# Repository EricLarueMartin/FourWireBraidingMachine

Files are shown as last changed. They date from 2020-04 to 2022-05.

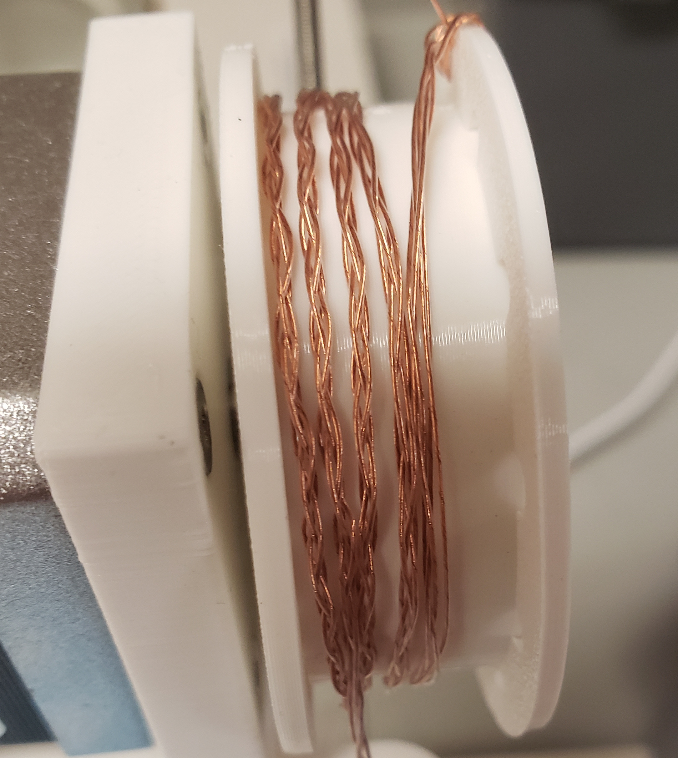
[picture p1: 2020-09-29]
Documentation/NoKinks.jpg

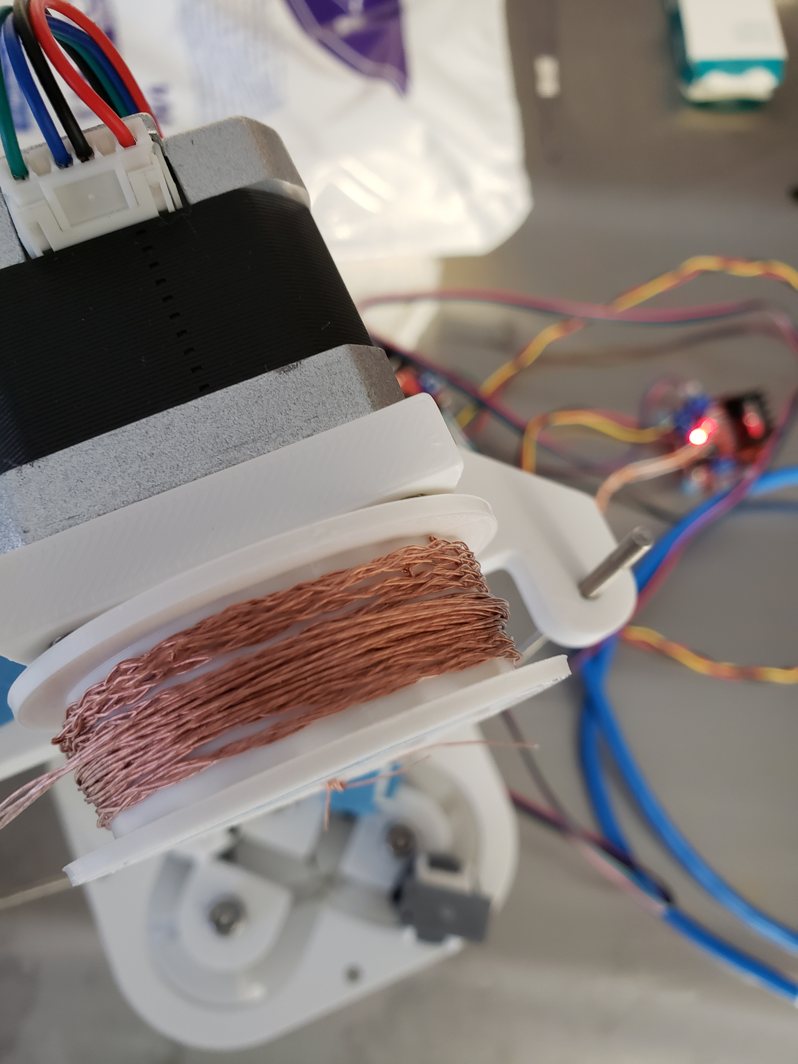
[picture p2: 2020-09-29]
Documentation/20200612_144232 1.jpg

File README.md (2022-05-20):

# FourWireBraidingMachine
Four wire braiding machine constructed out of widely available or printed parts.

Uses four horn gears to move four spool holders around on carriages. 
Design files for inventor included. Design could easily be extended for larger number of wires.

In addition to printed parts the following will be needed:

NEMA 17 stepper motors and drivers (L298N stepper motor driver boards were used, but anything compatible with Arduino is fine)

Arduino (Arduino Leonardo was used, but any Arduino is fine)

608 bearings (standard roller skate or skateboard bearings)

M8 threaded rod

M8 lock nuts (jam nuts could also be used)

M3 partially threaded bolts (for spool shaft)

M3 flathead bolts (must be flathead for gears to pass over bolt)

M3 threaded rods

M3 lock nuts (jam nuts could also be used)

Spring for clutch, SP-9702 was used but anything that fits and isn't too strong should work.

Spring for tips, 152-B from W.B. Jones Spring Co was used. Many other springs were found to work, but this is less tolerant than the clutch as it can't be adjusted.

**Ultem parts for ultra clean braiding:**

For the spools that go around the track:

4x SpoolHolderGuide

4x SpoolHolderRiser

4x SpoolSinglePieceTraditionalMachining — this is a remake of Spool designed for traditional machining.

For the winder:

1x WinderBracketInsert

1x WinderSpoolSinglePieceTraditionalMachining — this is a remake of WinderSpool designed for traditional machining.

When using the braider with Ultem parts print WinderBracket without the insert. WinderBracket and WinderBracketInsert can be printed as a single piece if not using a clean insert.

This design is free to use under the Creative Commons license. https://creativecommons.org/licenses/by-nc-sa/4.0/

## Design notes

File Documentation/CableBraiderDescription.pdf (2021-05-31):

## Non-twisting Cable Braider

### Eric L. Martin

09/20/20

A non-twisting cable braider was designed for braiding the signal cables for the LEGEND experiment, which requires very low-noise signal transmission. The area between cables acts as an antenna, picking up noise proportional to the area enclosed by the cables from ambient electromagnetic radiation. Two methods of reducing pickup noise used by LEGEND are braiding cables and shielding cables. By braiding the cables alternating loops are formed, which will have alternating polarity of pickup noise from loop to loop. This causes signicant cancellation of pickup noise. Smaller loops formed by twisting the cable tighter tends to provide better noise reduction, and has the added benet of producing an easier to handle cable bundle. Shielding the signal conductor with a grounded shield also reduces pickup noise, but there is always some noise that makes it through the shieldespecially at low frequency where the skin depth is longer than shield thickness. In bundles of shielded cables, the shields themselves also become antenna loops and this pickup can be mitigated by braiding the cables. LEGEND is testing braided bundles of individually shielded coaxial cables.
The LEGEND cable braider uses spools on carriages that are moved around a track by horn gears. As it is weaved the nished cable is wound on another spool, and the relative speed at which the cable is wound compared to how frequently the spool carriages move around the track controls the braid pitch. Cable braiders employing spools being moved around a track by horn gears have been used for more than a century. The most popular type is a maypole pattern, formed by two groups of cable carriers moving in opposite directions around a rough circle. The carriers switch between the inside and outside track to weave a tube around the center. Another method is to pass pairs of cables through the center of the cable braid, cycling through pairs of cables. Such a design was patented in 1989 under US patent 4803909. When braiding only four cables, such as will be done for LEGEND, this pattern is identical to a maypole braiding pattern. If additional spools are added to the LEGEND braider it will closely resemble the 1989 design, but with a key improvement to preventing twisting the cables. Braiding the LEGEND signal cables on a machine similar to the 1989 style of braiding machine resulted in either braids with too long a braid pitch to be easily handled, or kinks in the braided cable as shown in gure 3.
As the spools are moved around the track they rotate one revolution per

1

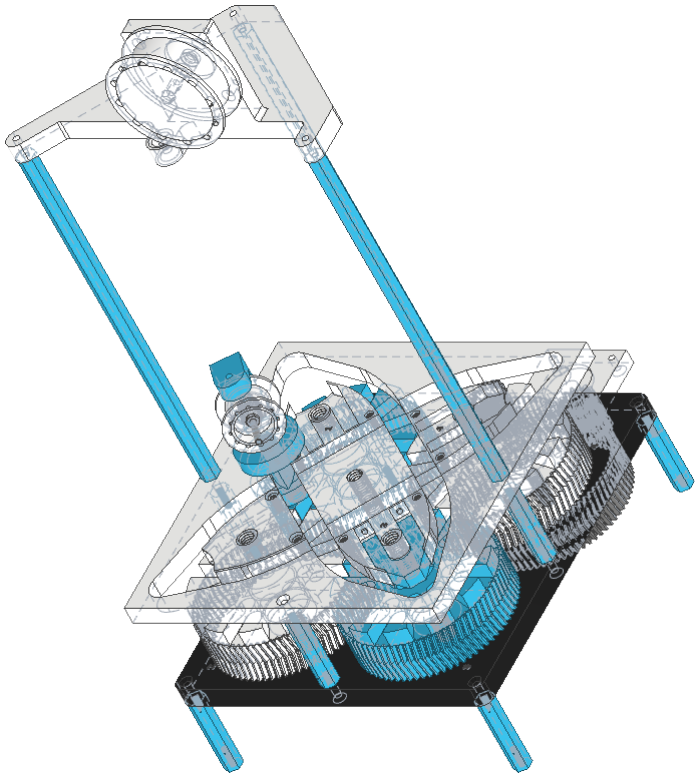
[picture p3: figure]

Figure 1: Non-twisting cable braider. Shown with one spool assembly, one spring tip on the lower right, and one tip cover on the lower left. Shafts, springs, motors, and most fasteners not shown.

2

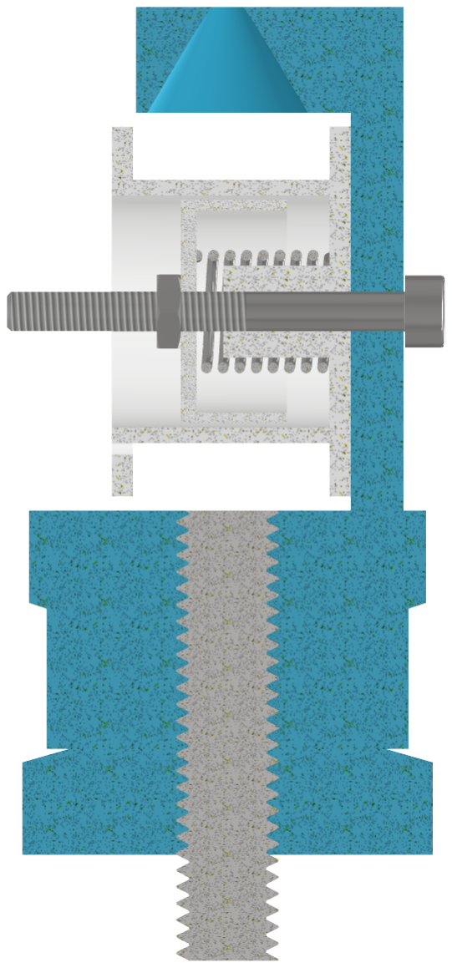
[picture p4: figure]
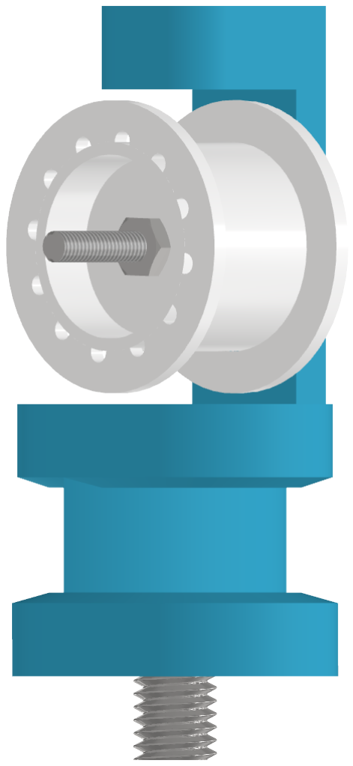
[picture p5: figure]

Figure 2: A spool assembly, half section view on the right. Cable is wound around the spool and the free end is threaded through the hole in the top of the spool holder. The spool rotates around a horizontal axle, this way no twisting of the cable occurs from unwinding the cable from the spool. The spring around the spool axle held by a bushing positioned by a lock nut applies force on the spool against the rising arm of the spool holder. Moving the lock nut adjusts the tension of the spool to prevent it from unwinding freely. An alternate design with a rewinder was considered to take up slack as the spool traveled through the central area of the track, but the slack didn't cause any issues so this simple friction clutch was used.

3

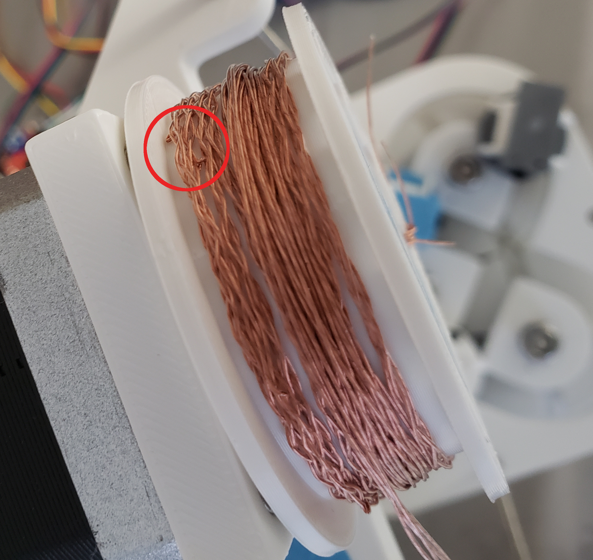
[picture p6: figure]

Figure 3: Kinks occurred when tightly braiding the LEGEND signal cables using a braiding machine that would twist the cables. Two such kinks are circled in red. Also shown on the spool is a section of cable that was braided with a longer braid pitch. While the longer braid pitch prevented kinks, the cable was dicult to handle.

4

trip around the track, twisting the cable once. This can be compensated for by taking the cable o the end results in one twist per loop removed from the spool. If the spools are wound such that the twist from cable coming o the spool cancels the twist from traversing the track there is no resulting twist in the cable. However, this requires the circumference of the spool matches the braid pitch. This would require a tightly wound spool for a tight cable braid, limiting the braid pitch by the minimum bending radius of the cable. This approach to eliminating cable twisting was unsuitable for attaining the high braid pitch desired for LEGEND.
To achieve a high braid pitch two improvements were made to the cable braider over the initial design.
Most importantly, the spools were oriented so cable was taken from the side instead of the end, so that there was no twisting induced by unwinding the cable from the spool (see gure 2). The track was redesigned to compensate for rotation of the spool as it traveled around the track (see gure 4). This counter rotation was induced by recesses added to the track. The recesses would catch the carriage guides and rotate the spools to compensate for the rotation due to movement around the track. Adding a retractable part of the track that the guide can push aside was found most eective, but rotation can be induced using a xed track with only recesses.
The second improvement was to shift the position of the spool carriages on the horn gears. In the previous design the slots in the horn gears were symmetric, causing two spools to be in the same position on opposite sides of the track. The carriages experience some positions of higher resistance, the most noticeable for the non-twisting cable braider is when pushing on the retractable track section. By shifting the spool positions (see gure 6) the machine only has to push a spool carriage through these dicult points one at a time instead of two at a time, reducing the torque required by the motor and allowing the machine to run faster. Breaking the symmetry of the track would have accomplished this as well but would have been more complicated.

5

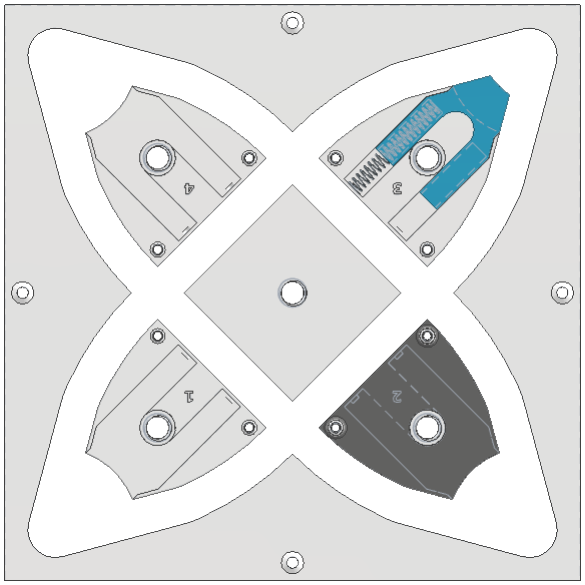
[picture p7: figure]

Figure 4: Track with rotation countering recesses at turning points. Only one of the spring-loaded retractable tips is shown in blue in the upper right, and only one cover is shown installed in gray in the lower right.

6

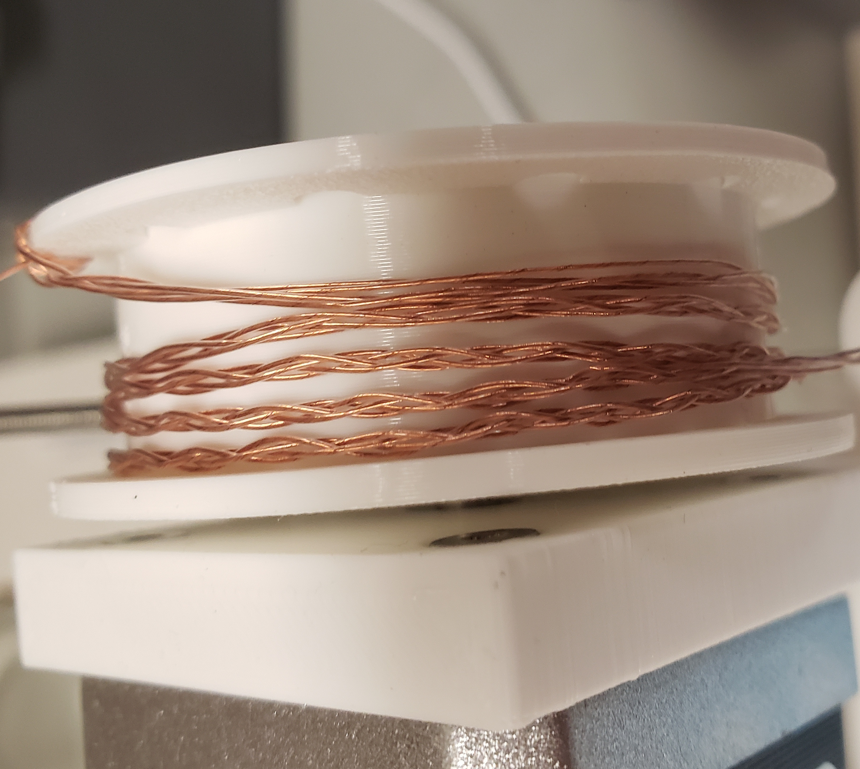
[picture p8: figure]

Figure 5: The same cable as in gure3 rebraided with the non-twisting cable braider.

7

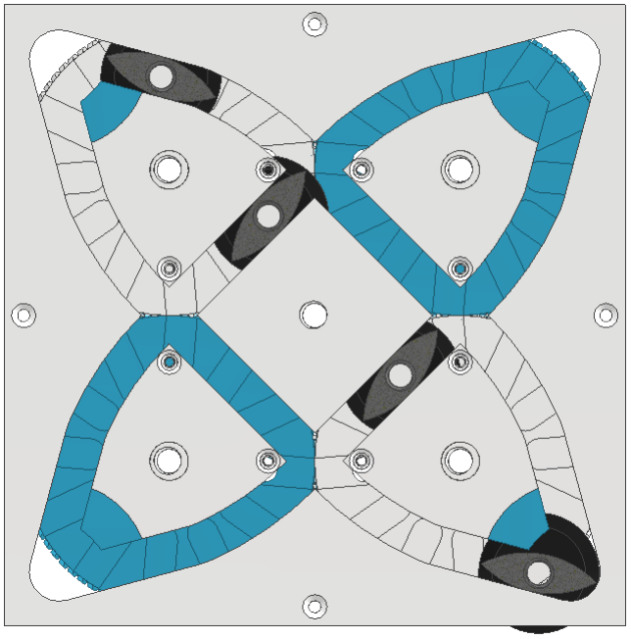
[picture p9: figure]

Figure 6: Additional slots were added to the horn gears to allow osetting the spools, so no more than one spool at a time passed the same problem point in the track. Preventing two spools from passing the rotation compensating corners at the same time is most important, as that is the highest resistance point in the movement. The carriage guide portion of the spool assemblies are shown in gray.

8

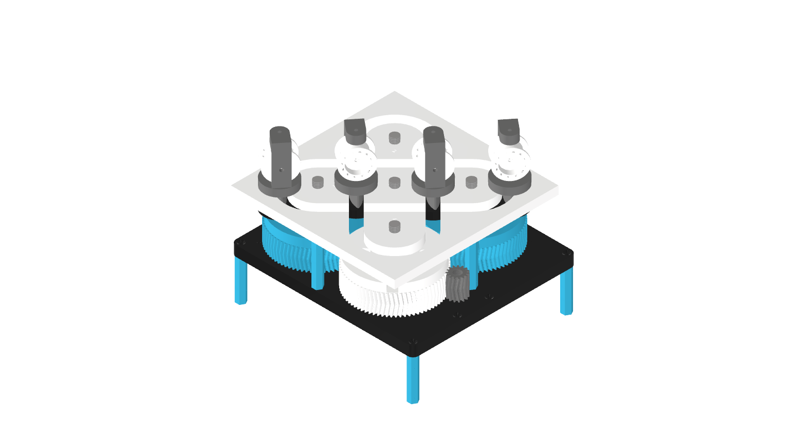
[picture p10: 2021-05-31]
Documentation/CableBraiderTwisting.png

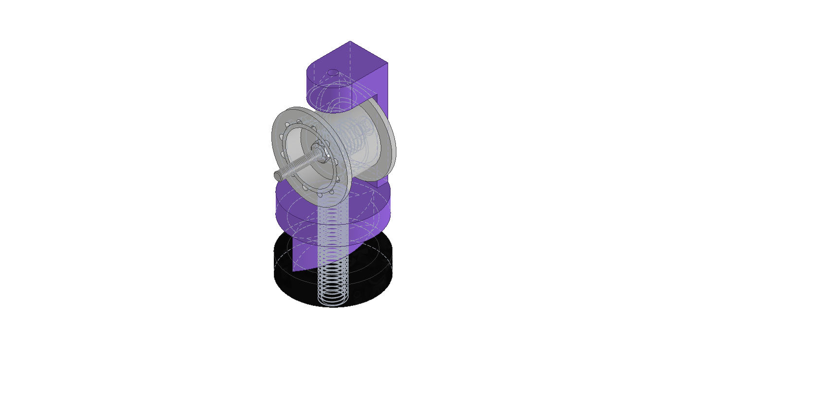
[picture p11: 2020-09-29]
Documentation/Carriage.png

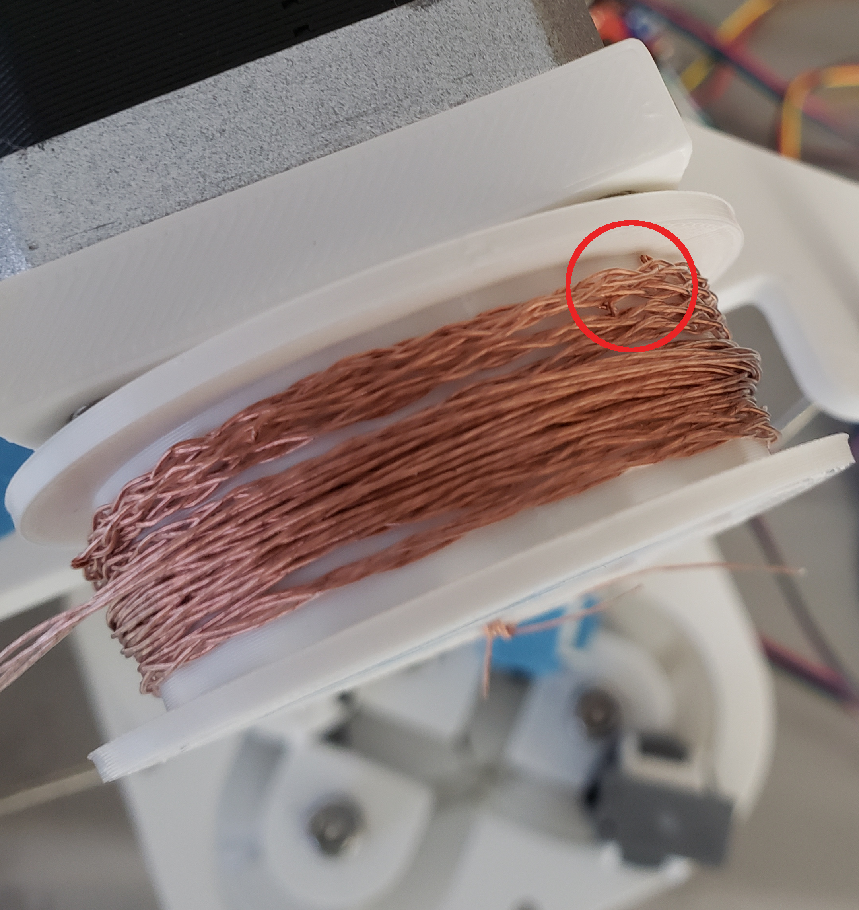
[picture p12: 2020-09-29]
Documentation/Kinks.jpg

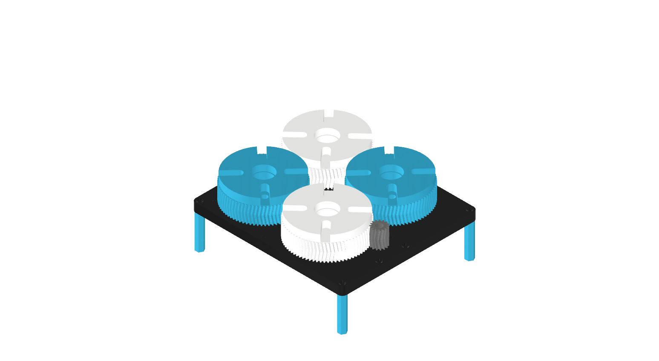
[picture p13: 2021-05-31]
Documentation/CableBraiderTwistingGears.png

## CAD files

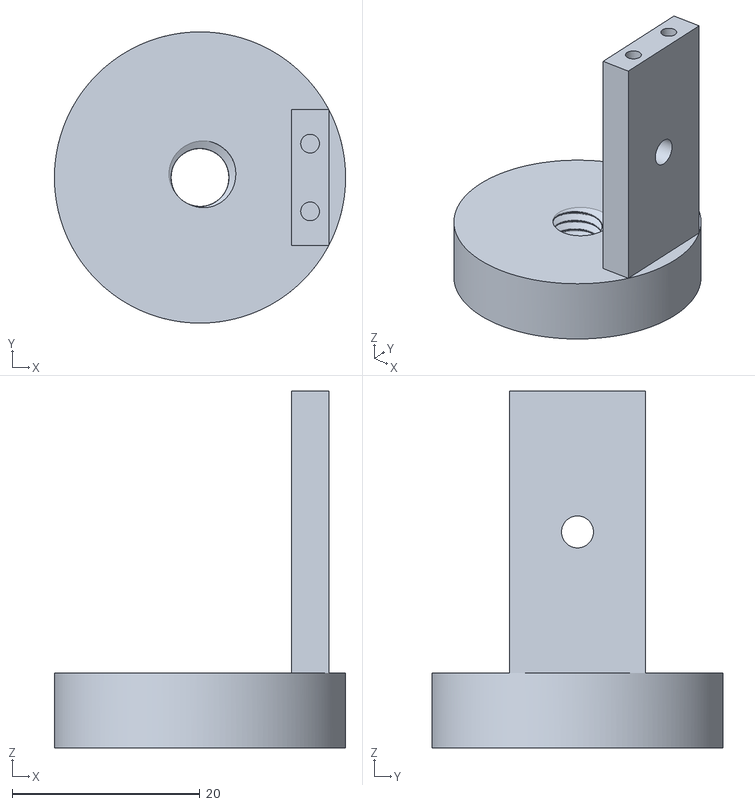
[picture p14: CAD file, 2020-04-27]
InventorFiles/SpoolHolder.stl
31.0 x 31.0 x 38.0

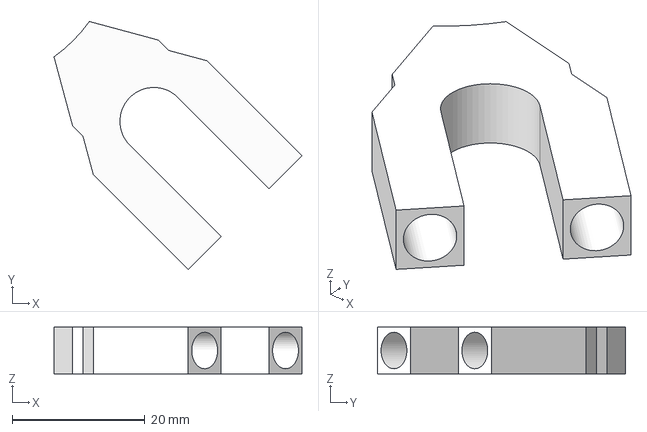
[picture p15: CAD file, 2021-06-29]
MetalPartStepFiles/GuidePlateTip.stp
37.3 x 37.3 x 7.00 mm

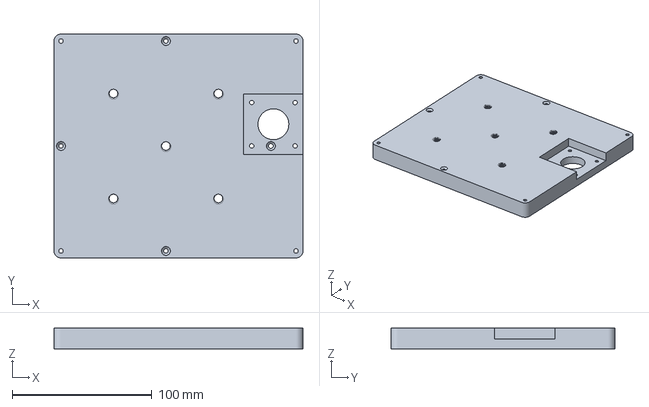
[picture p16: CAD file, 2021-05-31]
PrintingFiles/BasePlate.3mf
177.9 x 160.0 x 15.0 mm

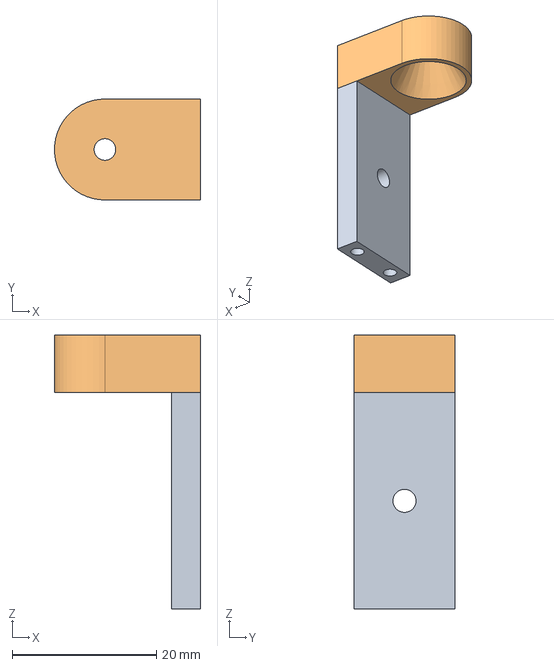
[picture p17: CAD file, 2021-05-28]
SpoolHolderRiserAndGuide.stp
20.3 x 14.0 x 38.0 mm

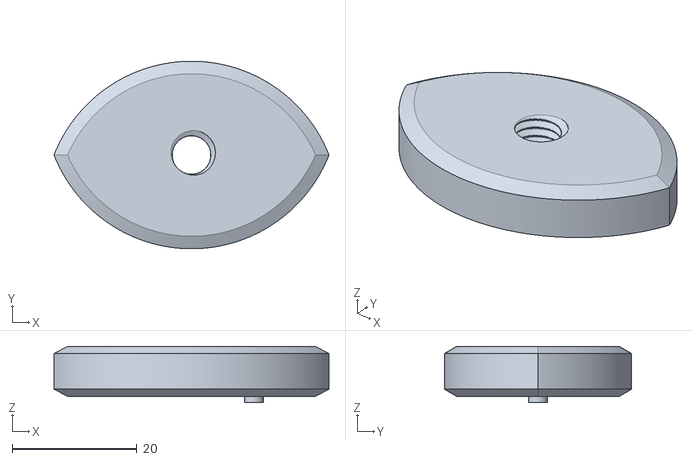
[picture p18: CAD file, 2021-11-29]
STLfiles/CarriagePlate.stl
44.0 x 30.0 x 9.00

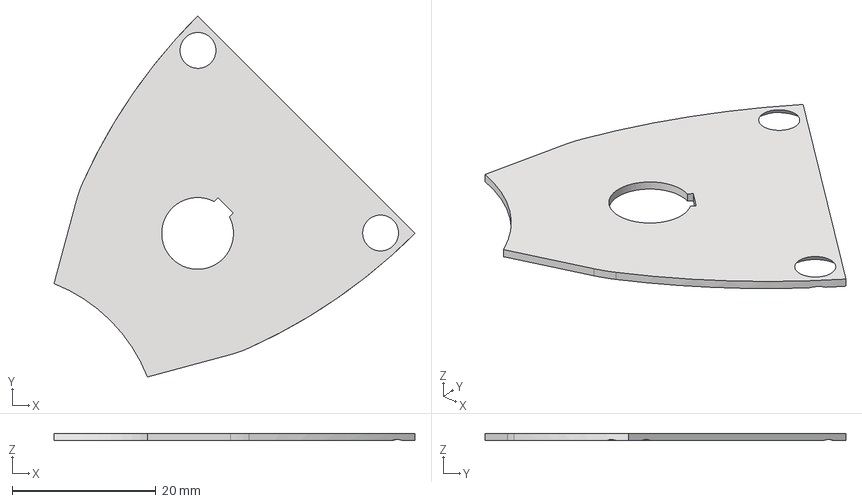
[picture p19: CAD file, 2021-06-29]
MetalPartStepFiles/GuidePlateCover.stp
50.3 x 50.3 x 1.00 mm

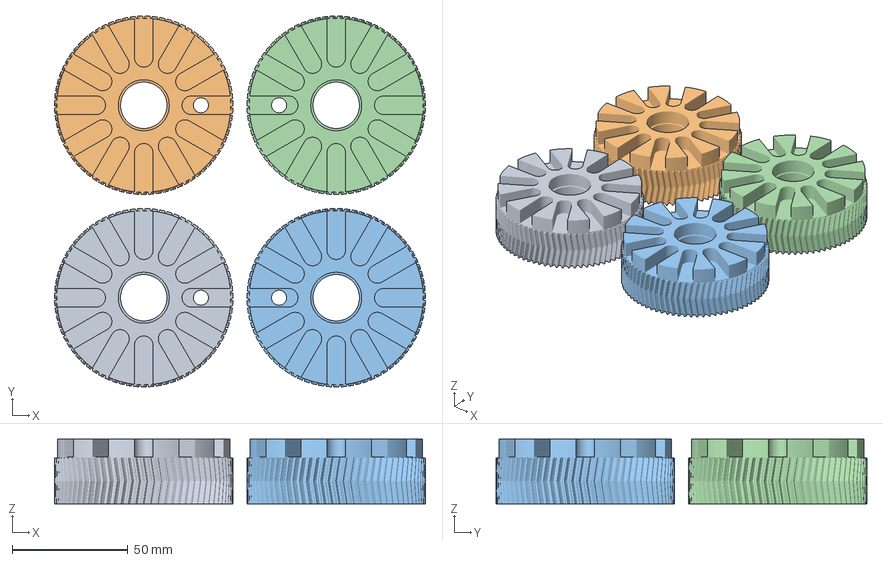
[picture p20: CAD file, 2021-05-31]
PrintingFiles/HornGearsMod1.3mf
160.0 x 160.0 x 28.0 mm
HornGearMod1.stl x 2

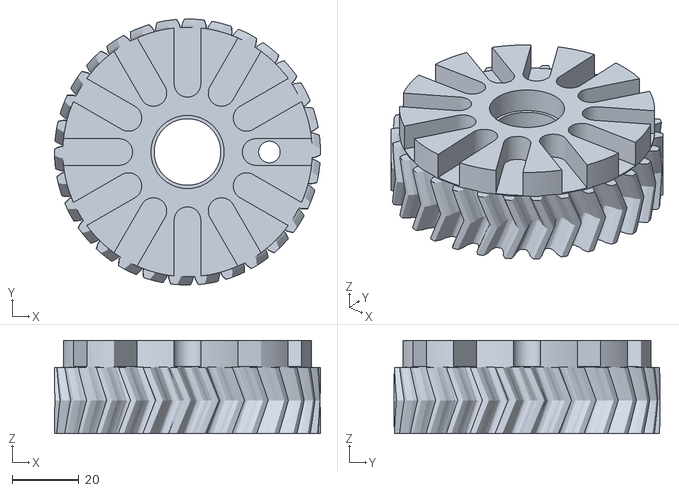
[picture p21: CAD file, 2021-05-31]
STLfiles/HornGearMod2.5.stl
80.0 x 80.0 x 28.0

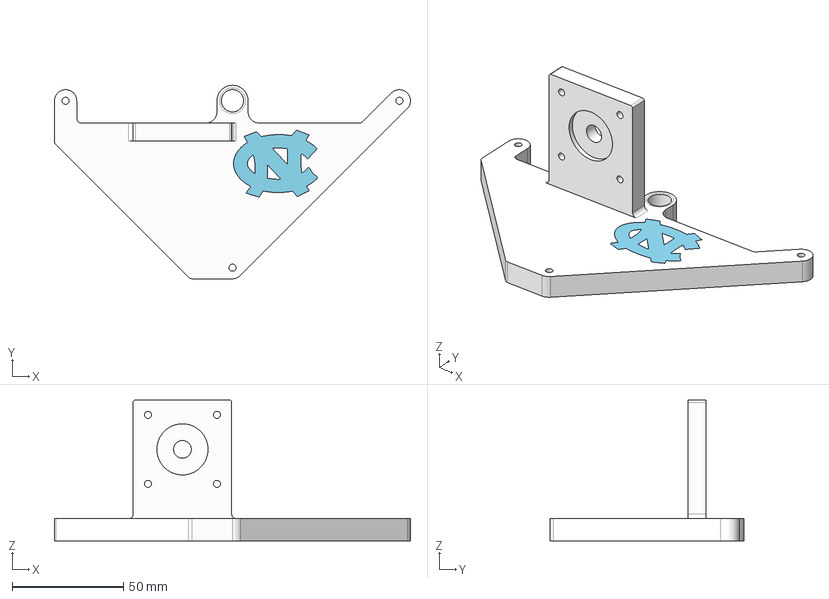
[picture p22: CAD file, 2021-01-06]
WinderBracket.stp
160.0 x 87.0 x 63.3 mm

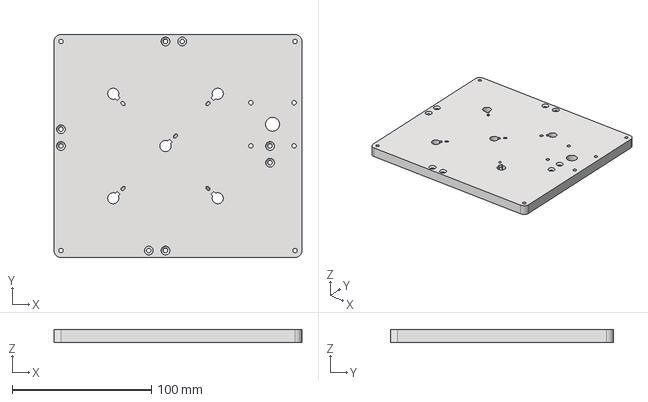
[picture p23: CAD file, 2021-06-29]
MetalPartStepFiles/BasePlate.stp
177.9 x 160.0 x 9.00 mm

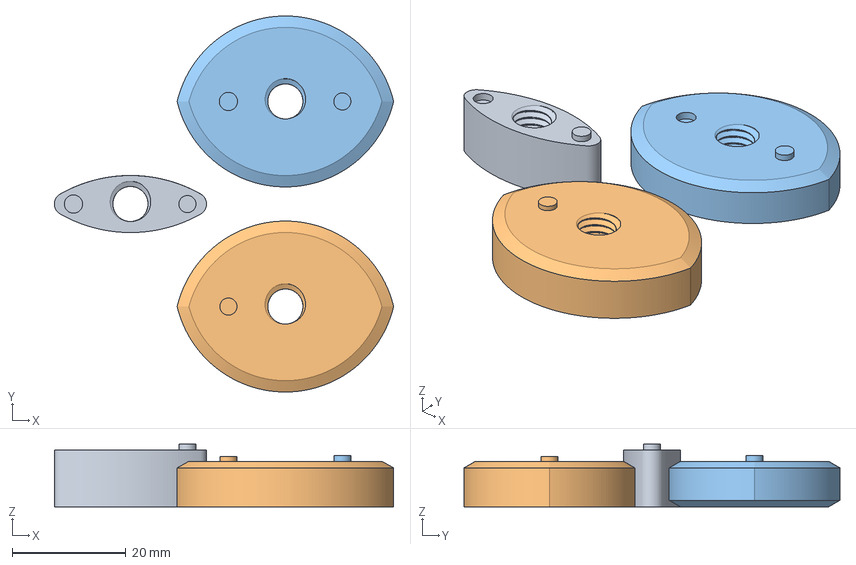
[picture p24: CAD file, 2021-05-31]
PrintingFiles/ThreePieceSpoolCarriageBase.3mf
59.6 x 66.0 x 11.0 mm
SpoolHolderGuide.stl
SpoolHolderBase.stl
CarriagePlate.stl

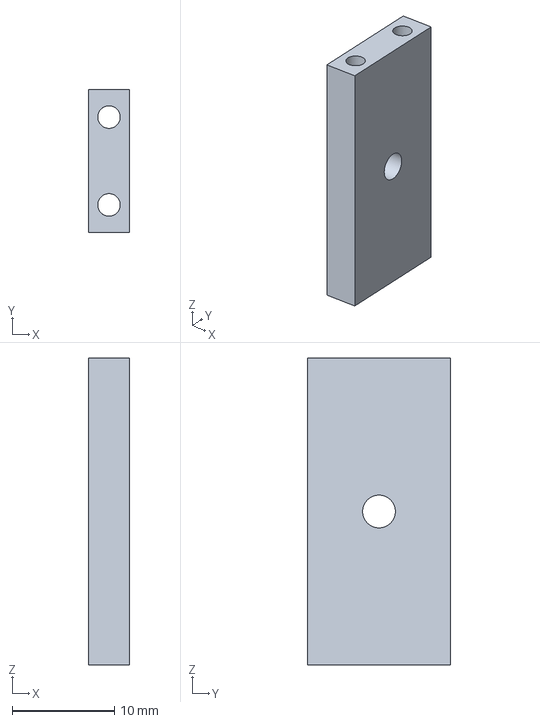
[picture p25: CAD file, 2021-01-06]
SpoolHolderRiser.stp
4.00 x 14.0 x 30.0 mm

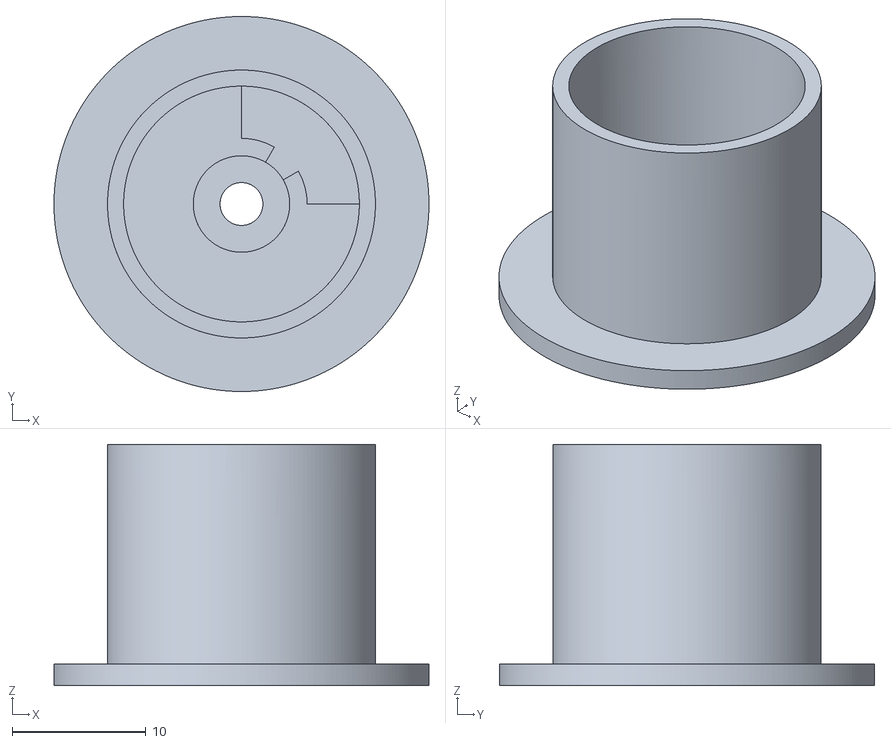
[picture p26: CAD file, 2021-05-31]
STLfiles/RewindingSpool.stl
28.0 x 28.0 x 18.0

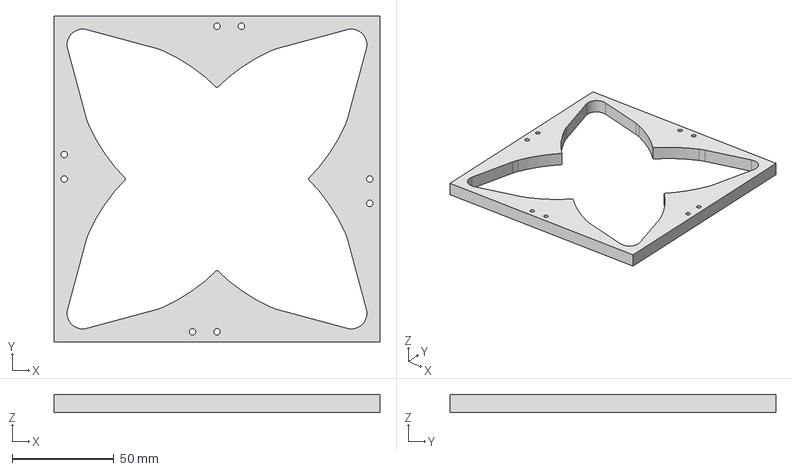
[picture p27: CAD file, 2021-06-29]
MetalPartStepFiles/GuidePlateOuter.stp
160.0 x 160.0 x 9.00 mm

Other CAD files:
PrintingFiles/BasePlateMetal.3mf
STLfiles/GuidePlateV1Center.stl
WinderBracketInsert.stp
MetalPartStepFiles/HornGearShaft.stp
Documentation/GuideDemo.iam
Documentation/OldVersions/GuideDemo.0002.iam
InventorFiles/17HS15-1504S-X1ShaftPlate.ipt
InventorFiles/17HS4401ShaftPlate.ipt
InventorFiles/6cmM3Standoff.ipt
InventorFiles/AlignmentPlate.ipt
InventorFiles/BasePlate.ipt
InventorFiles/BasePlateMetal.ipt
InventorFiles/CableBraider.iam
InventorFiles/Carriage.iam
InventorFiles/CarriagePlate.ipt
InventorFiles/DIN 7991 - M8x65 Fully Threaded.ipt
InventorFiles/GuidePlate.ipt
InventorFiles/GuidePlateV0.ipt
InventorFiles/GuidePlateV1.ipt
InventorFiles/M6DriveGear.ipt
InventorFiles/M8AlignmentJig.ipt
InventorFiles/M8_34mmRod.ipt
InventorFiles/M8_72mmRod.ipt
InventorFiles/ReductionDriveGear.ipt
InventorFiles/ReductionGearBracket.ipt
InventorFiles/RewindingSpool.ipt
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

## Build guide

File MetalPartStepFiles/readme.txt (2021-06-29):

1x BasePlate
1x GuidePlateCenter
4x GuidePlateCorner
4x GuidePlateCover
1x GuidePlateOuter
4x GuidePlateTip
4x HornGearHorns
5x HornGearShaft

All parts in stainless steel except for GuidePlateTip, which should be a low friction material like teflon.

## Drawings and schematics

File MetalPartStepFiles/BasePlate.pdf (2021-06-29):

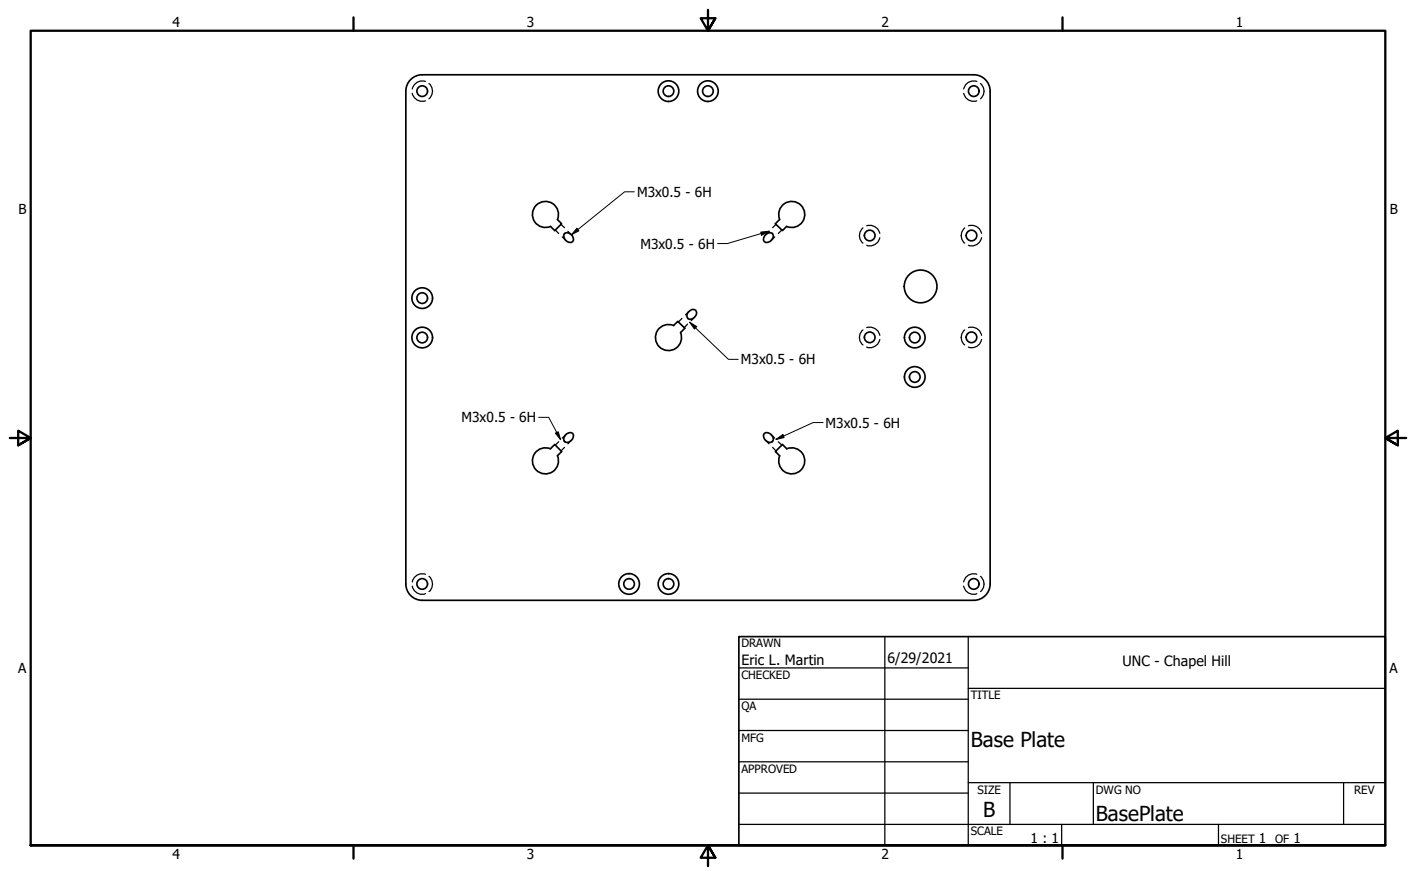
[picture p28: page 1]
Base Plate

DRAWN Eric L. Martin | 6/29/2021 | UNC - Chapel Hill

CHECKED

MFG

APPROVED

SIZE B | DWG NO BasePlate | REV

SCALE 1 : 1 | | SHEET 1 OF 1

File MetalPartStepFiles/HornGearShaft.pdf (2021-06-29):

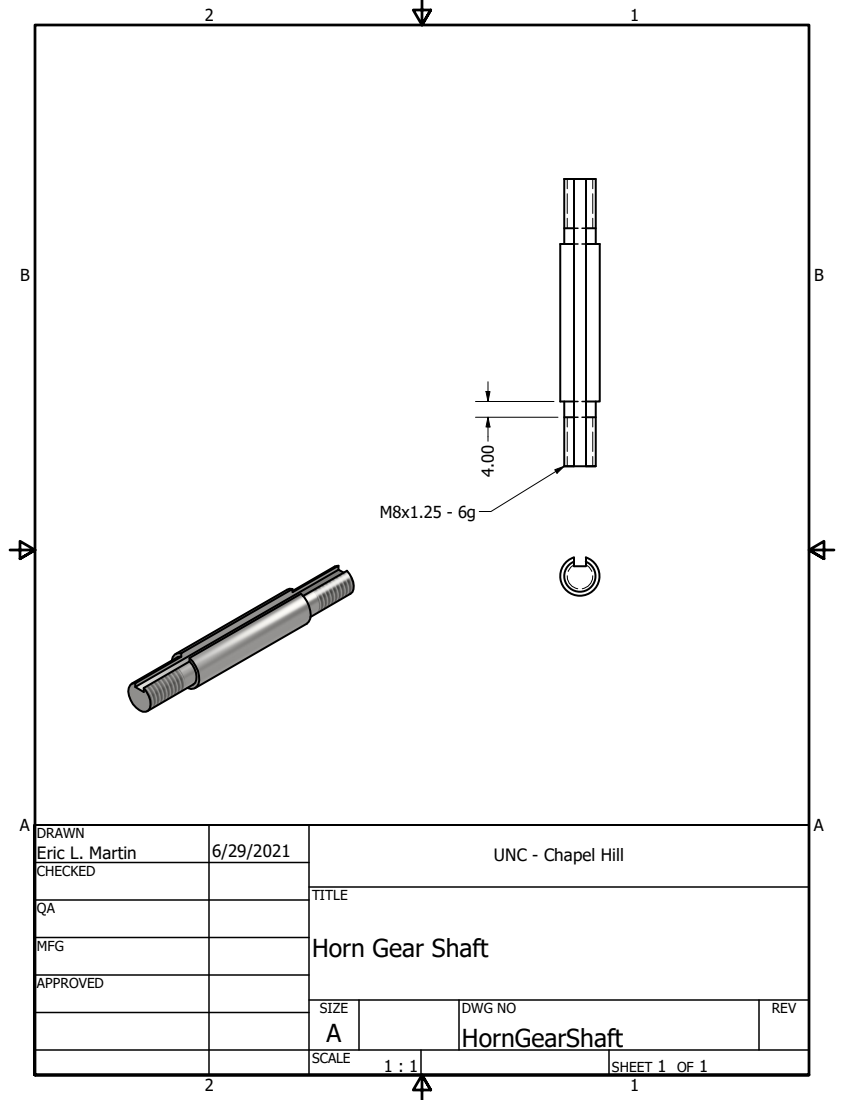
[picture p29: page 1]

DRAWN Eric L. Martin | 6/29/2021 | UNC - Chapel Hill

CHECKED

Horn Gear Shaft

MFG

APPROVED

SIZE A | DWG NO HornGearShaft | REV

SCALE 1 : 1 | | SHEET 1 OF 1

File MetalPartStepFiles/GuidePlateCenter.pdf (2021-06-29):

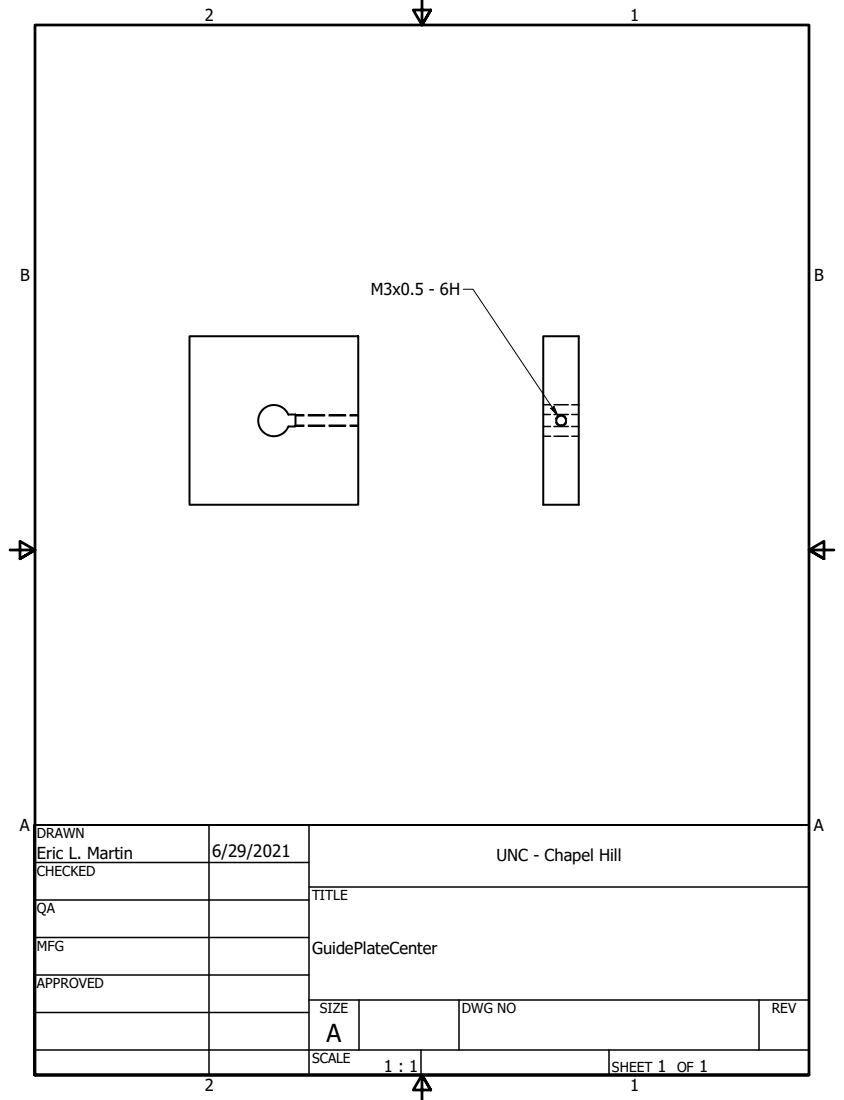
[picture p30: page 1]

DRAWN Eric L. Martin | 6/29/2021 | UNC - Chapel Hill

CHECKED

MFG

APPROVED

SIZE A | DWG NO | REV

SCALE 1 : 1 | | SHEET 1 OF 1

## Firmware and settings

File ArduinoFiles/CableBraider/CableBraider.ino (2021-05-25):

// length unit is left off in names of variables, as it doesn't really matter to the program, but the constants were set for centimeters and seconds

// Include the AccelStepper library:
#include <AccelStepper.h>
#include <MultiStepper.h>
// Define the AccelStepper interface type:
#define MotorInterfaceType 4

// physical values used to calculate stepper speeds
const int HornGearTeeth = 30; // 30  
const float ReductionRatio = 5; // reduction ratio on braiding drive gear
const int DriveGearTeeth = 6;
const int BraiderStepsPerRevolution = 200;
const int WinderStepsPerRevolution = 200;
const float RevolutionsPerBraid = 2.0; // revolutions of horn gear to make a complete braid cycle
const float WinderCircumference = 4.5 * 3.14159265; // in centimeters 

// constants that depend on other constants

const float StepsPerDistance = WinderStepsPerRevolution/WinderCircumference; // steps per distance unit (cm) on winder
const float StepsPerBraid = BraiderStepsPerRevolution*HornGearTeeth*ReductionRatio/DriveGearTeeth*RevolutionsPerBraid; // steps to complete a braiding cycle

// ratio of braiding stepper motor to winding gear to get one braid per centimeter
const float StepRatio =  StepsPerBraid/StepsPerDistance;


class cableBraider
{
 public: 

  AccelStepper *braiderStepper,*winderStepper;
  MultiStepper *steppers;

  // user adjusted settings and defaults
  float windingSpeed = 0.6; // one distance unit (cm) per second
  float braidsPer = 0.25; // per distance unit (cm)
  float braiderAcceleration = 25.0; // acceleration of braider in steps per second squared
  int braidDirection = 1; // braiding motor turning direction

  int braidPin = 13; // default is all braiders run if pin 13 is grounded
  
  // values calculated based on user adjuted settings
  
  // speed stepper motors run at in steps per second
  float winderStepSpeed; // = windingSpeed/WinderCircumference*WinderStepsPerRevolution; 
  float braiderStepSpeed; // = winderStepSpeed * stepRatio * braidsPer;
  
  // run control
  bool bRunning = false;
  bool outputsEnabled = false;
  bool freeRunning = false;
  float cableLength; // target cable length

  char machineName[40] = "";

  cableBraider(int pins[8], char setName[40]); // constructor sets defaults
  void braidCable();
  void cableBraider::haltSteppers();
  void cableBraider::recalc();
  void cableBraider::displaySettings();
  void cableBraider::displayPosition();

};

/* pins for MotorInterfaceType = 4 (FULL4WIRE)
0-3 - winder L298N pins 1-4
4-8 - braider L298N pins 1-4   
*/
cableBraider::cableBraider(int pins[8], char setName[40] = "") // constructor sets defaults
{
  winderStepper = new AccelStepper(MotorInterfaceType,pins[0],pins[1],pins[2],pins[3]);
  braiderStepper = new AccelStepper(MotorInterfaceType,pins[4],pins[5],pins[6],pins[7]);

  steppers = new MultiStepper;

  steppers->addStepper(*winderStepper);
  steppers->addStepper(*braiderStepper);

  // this part should be redundant, but just in case
//  windingSpeed = 0.3;
//  braidsPer = 0.3;
//  braiderAcceleration = 25.0;
//  braidDirection = 1;
  braidPin = 13;
  bRunning = false;
  cableLength = 0.0;
  outputsEnabled = false;
  memcpy(machineName,setName,40);
}

void cableBraider::braidCable() {
  // Set target position:
  winderStepper->enableOutputs();
  braiderStepper->enableOutputs();
  outputsEnabled = true;
  long absolute[2];
  absolute[0] = cableLength*StepsPerDistance; // set target winder position
  absolute[1] = braidDirection*cableLength*StepsPerDistance*braiderStepSpeed/winderStepSpeed; // braider position required to maintain braid ratio
  // use the current position as the starting position
  winderStepper->setCurrentPosition(0);
  braiderStepper->setCurrentPosition(0);
  // Run to position with set speed and acceleration:
  Serial.print(machineName);
  Serial.print(" stepping to position ");
  Serial.print(cableLength);
  Serial.print(" cm. ( ");
  Serial.print(absolute[0]);
  Serial.print(" / ");
  Serial.print(absolute[1]);
  Serial.println(" )");      
  // set steppers to run for desired cable length
//  delay(100);
  steppers->moveTo(absolute);
}

void cableBraider::haltSteppers()
{
  Serial.print("Stopping steppers on ");
  Serial.print(machineName);
  Serial.println(".");
  winderStepper->stop();
  braiderStepper->stop();
  bRunning = false;
  displayPosition();
  winderStepper->disableOutputs();
  braiderStepper->disableOutputs();
  outputsEnabled = false;
}

// recalculate the stepping speeds after parameter change
void cableBraider::recalc() 
{
  if (bRunning) haltSteppers();
  winderStepSpeed = windingSpeed*StepsPerDistance; 
  braiderStepSpeed = winderStepSpeed * StepRatio * braidsPer;
  winderStepper->setMaxSpeed(winderStepSpeed);
  winderStepper->setSpeed(winderStepSpeed);
  winderStepper->setAcceleration(braiderAcceleration/(StepRatio*braidsPer));
  braiderStepper->setMaxSpeed(braiderStepSpeed);
  braiderStepper->setSpeed(braiderStepSpeed);
  braiderStepper->setAcceleration(braiderAcceleration);
}

void cableBraider::displaySettings()
{
  Serial.println(machineName);
  Serial.print("braidsPer = ");
  Serial.println(braidsPer);
  Serial.print("windingSpeed = ");
  Serial.println(windingSpeed);
  Serial.print("winderStepSpeed = ");
  Serial.println(winderStepSpeed);
  Serial.print("braiderStepSpeed = ");
  Serial.println(braiderStepSpeed);
  Serial.print("braiderAcceleration = ");
  Serial.println(braiderAcceleration);
  Serial.print("braidDirection = ");
  Serial.println(braidDirection);
}

void cableBraider::displayPosition() 
{
  Serial.print(machineName);
  Serial.print("'s position is ");
  Serial.print(winderStepper->currentPosition()/StepsPerDistance);
  Serial.print(" cm. ( ");
  Serial.print(winderStepper->currentPosition());
  Serial.print(" / ");
  Serial.print(braiderStepper->currentPosition());
  Serial.println(" )");      
}

const int NumBraiders = 1;
const int BraiderPins[NumBraiders][8] = {
  {4,5,6,7,8,9,10,11} // pins for first braider
  };
const char MachineNames[NumBraiders][40] = {
  "Prototype B (0)"
};
  
cableBraider *braider[NumBraiders];

void setup() {
// start serial port at 9600 bps
  Serial.begin(9600);

// wait for serial port to connect. Needed for native USB port only
  pinMode(13,INPUT_PULLUP); // set the external run pin to pullup mode, so it will read high unless shorted to ground
  for (int ctDelay = 0; !Serial; ++ctDelay) { 
    if (ctDelay>10 && !digitalRead(13)) break; // if the external run pin is shorted to ground, just wait a short time to initialize to be sure then go without serial
    delay(1); 
    }
  if (Serial)
  {
    Serial.print("StepsPerDistance = ");
    Serial.println(StepsPerDistance);
    Serial.print("StepsPerBraid = ");
    Serial.println(StepsPerBraid);
    Serial.print("Ratio for 1 braid per cm = ");
    Serial.println(StepRatio);
    Serial.println("A          : set acceleration of braiding motor in steps pre second squared.");
    Serial.println("B          : set braid density in braids per centimeters.");
    Serial.println("S          : set winding speed in centimeters per second.");
    Serial.println("D          : change braiding motor direction.");
    Serial.println("?          : display settings.");
    Serial.println("P          : report position in centimeters.");
    Serial.println("H          : halt motors.");
    Serial.println("R <length> : run to braid length of cable in centimeters.");
  }

  for (int ct = 0; ct < NumBraiders; ++ct) 
  {
    braider[ct] = new cableBraider(BraiderPins[ct],MachineNames[ct]);
    braider[ct]->recalc();
    braider[ct]->displaySettings();
  }
}

void loop() {
  while (!Serial.available())
    for (int ctBraider = 0; ctBraider < NumBraiders; ++ctBraider)
    {
      if (braider[ctBraider]->bRunning) // was running
      {
        braider[ctBraider]->bRunning = braider[ctBraider]->steppers->run();
        if (!braider[ctBraider]->bRunning && digitalRead(braider[ctBraider]->braidPin)) { // did it stop and braidPin is open?     
          braider[ctBraider]->displayPosition();
          braider[ctBraider]->winderStepper->disableOutputs();
          braider[ctBraider]->braiderStepper->disableOutputs();
        }          
      }
      else if (!digitalRead(braider[ctBraider]->braidPin)) // run for 1 cm if braidPin grounded
      {
        braider[ctBraider]->cableLength = 1.0;
        braider[ctBraider]->braidCable();
        braider[ctBraider]->bRunning = true;
      }
  } 
  static int nBraider = 0;
  char arg = Serial.read();
  switch (toUpperCase(arg)) {
    case 'M' :
      nBraider = Serial.parseInt();
      if (nBraider >= NumBraiders)
        nBraider = 0;
      Serial.print("Braiding machine ");
      Serial.print(nBraider);
      Serial.println(" selected.");  
      braider[nBraider]->displaySettings();
      break;
    case 'R' :
      braider[nBraider]->cableLength = Serial.parseFloat();
      Serial.print("Braiding for ");
      Serial.print(braider[nBraider]->cableLength);
      Serial.println(" cm.");  
      braider[nBraider]->braidCable();
      braider[nBraider]->bRunning = true;
      break;
    case 'B' :
      braider[nBraider]->braidsPer = Serial.parseFloat();
      Serial.print("Braid density set to ");
      Serial.print(braider[nBraider]->braidsPer);
      Serial.println(" braids per cm.");  
      braider[nBraider]->recalc();
      braider[nBraider]->displaySettings();
      break;
    case 'S' :
      braider[nBraider]->windingSpeed = Serial.parseFloat();
      Serial.print("Winding speed set to ");
      Serial.print(braider[nBraider]->windingSpeed);
      Serial.println(" cm/s.");  
      braider[nBraider]->recalc();
      braider[nBraider]->displaySettings();
      break;
    case 'A' :
      braider[nBraider]->braiderAcceleration = Serial.parseFloat();
      Serial.print("Braider acceleration set to ");
      Serial.print(braider[nBraider]->braiderAcceleration);
      Serial.println(" steps/s^2.");  
      braider[nBraider]->recalc();
      braider[nBraider]->displaySettings();
      break;
    case '?' :
      braider[nBraider]->displaySettings();
      break;
    case 'P' :
      braider[nBraider]->displayPosition();
      break;
    case 'H' :
      braider[nBraider]->haltSteppers();
      break;      
    case 'D' :
      braider[nBraider]->braidDirection*=-1;
      braider[nBraider]->displaySettings();
      break;
  }
}

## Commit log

2020-04-27 Initial commit.
    [Carriage.iam, CarriageGuide.ipt, CarriageGuide.stl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]
2020-05-22 Added UNC logo to winder bracket. Go Tar Heels!
    [FourWireWinderBracket.0009.ipt, FourWireWinderBracket.ipt, FourWireWinderBracket.stl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]
2020-05-23 Added old Well to winder spool.
    [NEMA17.ipt, WinderAssembly.iam, WinderSpool.ipt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]
2020-05-26 Added Old Well logo to winder spool.
    [OldWell.dxf, ShaftPlate.ipt, ShaftPlate.stl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]
2020-06-05 Added filled in labels to guide plate parts. This will result in fewer crevices for dirt.
    [DoubleHelicalHornGear.ipt, DoubleHelicalHornGearMirror.ipt, FourWireLitzBasePlate.ipt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]
2020-06-05 Modified so a braider is a class, making running multiple braiders on a single Arduino easier. Added option to ground a pin to run braider, so an Arduino can be programmed to run a braiders off a swi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
2020-06-08 Redid braiding on pin grounded to run at same speed as using serial. For some reason the speed isn't right, though the settings appear to be, but at least now both modes of running have the same resu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
2020-07-27 Modification for not twisting.
    [17HS15-1504S-X1ShaftPlate.ipt, 17HS4401ShaftPlate.ipt, BasePlate.ipt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]
2020-09-29 Many changes.
    [6cmM3Standoff.ipt, 8mmClamp.ipt, 8mmClamp.stl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]
2020-10-22 Version 1
    [DriveGearGripper.ipt, GuidePlateV2.ipt, GuidePlateV3.ipt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]
2020-10-29 Generated step file.
    [CableBraider.iam, GuidePlateV2.ipt]
2020-11-19 Added swivel tip option.
    [CableBraider.iam, GuidePlateV0.ipt, GuidePlateV2.ipt]
2021-01-06 Modified guide plate to add a Teflon insert for spring loaded tips (V1). Modified spool carriage to better stay in track. Modified winder to allow Ultem insert. Added a sub plate to hold electronics.
    [AlignmentPlate.ipt, BasePlate.ipt, CableBraider.iam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]
2021-01-06 Minor modificatio to winder spool to allow manufacturing from machining rather than additive manufacturing.
    [CableBraider.iam, Carriage.iam, CarriageGuide.ipt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]
2021-01-06 Added single piece models for the spools suitable for traditional machining.
    [Spool.ipt, Spool.stp, SpoolHolderGuide.stp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]
2021-01-14 Changed reduction gear ratio to 1 and reversed default direction.
    [CableBraider.ino]
2021-01-14 Modified winder bracket to have separate insert for cable guide.
    [WinderBracket.ipt]
2021-03-05 Commit before mods to base plate thickness
    [BasePlate.ipt, Carriage.iam, ElectronicsPlate.ipt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]
2021-03-08 Changed module to 1 mm. Thickened baseplate.
    [BasePlate.ipt, Carriage.iam, CarriagePlate.ipt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]
2021-03-17 Lengthened carriage rod
    [Carriage.iam, M8_34mmRod.ipt]
2021-03-18 Modification to carriage post.
    [Carriage.iam, M8_34mmRod.ipt]
2021-04-12 Mount for NEMA 17 now 2.2 mm deep.
    [ReductionGearBracket.ipt]
2021-04-29 Added part to keep gears from rotating for assembly.
    [GearLock.ipt, ShaftPlate.ipt]
2021-04-30 Changed NEMA17 shaft holes to 6 mm and modified drive gear gripper for more clearance.
    [DriveGearGripper.ipt, ReductionGearBracket.ipt, WinderBracket.ipt]
2021-05-01 Added alignment jig for spring tips on shaft.
    [M8AlignmentJig.ipt]
2021-05-25 Added slit to winder for insert. Added winder spool removal aid.
    [WinderBracket.ipt, WinderSpoolRemovalAid.ipt]
2021-05-28 Adding metal parts mod
    [BasePlateMetal.ipt, SpoolHolderRiserAndGuide.stp, WinderAssembly.iam]
2021-05-29 Added removal aid for winder spool
    [WinderSpoolRemovalAid.ipt]
2021-05-31 Adding metal version parts
    [AlignmentPlate.stl, BasePlate.3mf, BasePlateBearingCover.stl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]
2021-06-01 Mods for metal braider
    [Carriage.iam, GuidePlateMetal.ipt, MetalCableBraider.iam]
2021-06-02 Rotated threads on tips to be identical.
    [BasePlate.ipt, GuidePlateV2.ipt, GuidePlateV3.ipt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]
2021-06-02 Moved metal braider to separate directory.
    [BasePlate.ipt, CableBraider.iam, Carriage.iam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]
2021-06-02 Revised metal cable braider design to use shafts for horn gears with shoulders and flats.
    [BasePlate.ipt, CableBraider.iam, Carriage.iam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]
2021-06-02 Added shaft and metal version of carriage.
    [BasePlate.ipt, CableBraider.iam, GuidePlate.ipt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]
2021-06-09 Rotated flats and added set screws.
    [BasePlate.ipt, CableBraider.iam, GuidePlate.ipt]
2021-06-11 Modified interior corners to make parts machinable with a 2mm diameter endmill.
    [BasePlate.ipt, CableBraider.iam, GuidePlate.ipt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]
2021-06-21 Changed clearance on carriage guide to reflect this no longer sanded printed plastic.
    [SpoolHolder.ipt]
2021-06-21 Added standoffs.
    [BasePlate.ipt, CableBraider.iam, GuidePlate.ipt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]
2021-06-22 Modified to use keyways instead of D shapes.
    [BasePlate.ipt, CableBraider.iam, Carriage.iam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]
2021-06-29 Added step files with drawings for threads for machined parts.
    [BasePlate.idw, BasePlate.ipt, BasePlate.stp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]
2021-10-12 fixed Standoff.ipt
    [Standoff.ipt]
2021-10-12 Extended carriage length 3 mm on each end.
    [Carriage.iam, CarriagePlate.ipt, SpoolHolder.ipt]
2021-10-23 Added assembly aid.
    [GuidePlate.ipt]
2021-11-29 Reshaped Carriage.iam
    [Carriage.iam, CarriagePlate.ipt, CarriagePlate.stl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]
